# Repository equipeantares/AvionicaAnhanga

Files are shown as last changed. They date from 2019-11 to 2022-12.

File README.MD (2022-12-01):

# Base de Acionamento

## Introdução 

### Motivação

A equipe Antares de espaçomodelismo da Unicamp tem como um de seus projetos desenvolvidos o foguete Aurora. Trata-se de um foguete de propulsão sólida com apogeu esperado de 3km. Como parte dos requisitos necessários para ter sucesso na missão, o foguete precisa de um sistema de aviônica que será responsável por coletar dados e tomar decisões previamente programadas durante o voo. Com o objetivo de monitorar o estado do foguete antes, durante e depois do lançamento, é necessário ter um sistema em solo que seja capaz de receber os dados coletados pela aviônica, permitindo que os presentes tenham informações em tempo real. Além disso, esse sistema deve permitir que o acionador do motor seja ligado de forma segura durante o lançamento, não expondo pessoas a riscos.

### Objetivo

Sendo assim, o objetivo deste projeto é desenvolver um sistema de controle de base para o foguete, o qual deve ser capaz de iniciar o lançamento de forma segura e robusta e capaz de receber e apresentar dados da telemetria do voo colhidos pela aviônica.

### Soluções comerciais

Pelo fato de o sistema precisar ser personalizado, se ajustando ao sistema presente no foguete e aos demais requisitos específicos do projeto, não existem alternativas comerciais que cumpram integralmente o objetivo.

## Especificação
    - Microcontrolador: o dispositivo deverá ser capaz de fazer processamentos lógicos, sendo assim necessário um microcontrolador. Por motivos de acessibilidade e familiaridade, será utilizada a plataforma Arduino no MCU ESP-8266 12F.

    - Comunicação e dados: com o objetivo de receber dados de telemetria do foguete, o dispositivo deverá ter um sistema transceptor, que será implementado por um módulo LoRA E32-915T20D.

    - Interface: como interface, o dispositivo contará com pinos auxiliares para monitoramento do funcionamento da placa e pinos de seleção de função para alimentação e modo de acionamento da ignição, sendo a seleção feita por meio de jumpers.

    - Ignição: deverá suportar dois modos de acionamento do circuito ignitor: por sinal elétrico e por comando remoto. O modo será escolhido via inserção manual de jumpers antes do lançamento.

    - Alimentação: o sistema deverá ter interface de alimentação, podendo operar com a alimentação interna de 3V3 ou alimentação externa de 5V.

## Diagrama

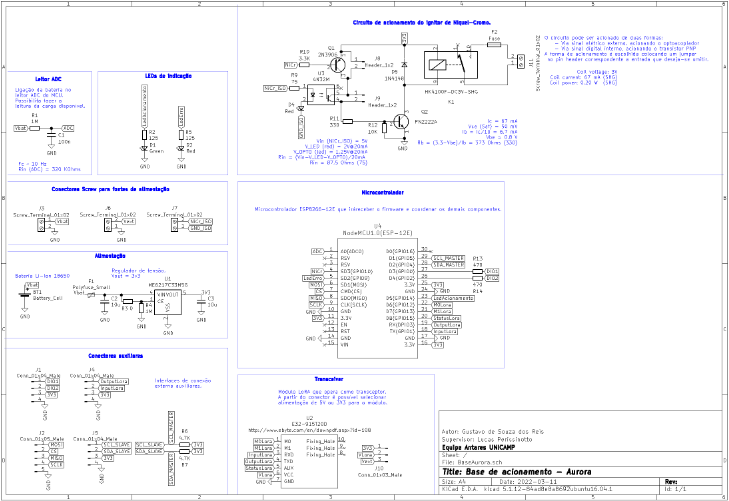
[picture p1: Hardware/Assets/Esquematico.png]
Esquematico


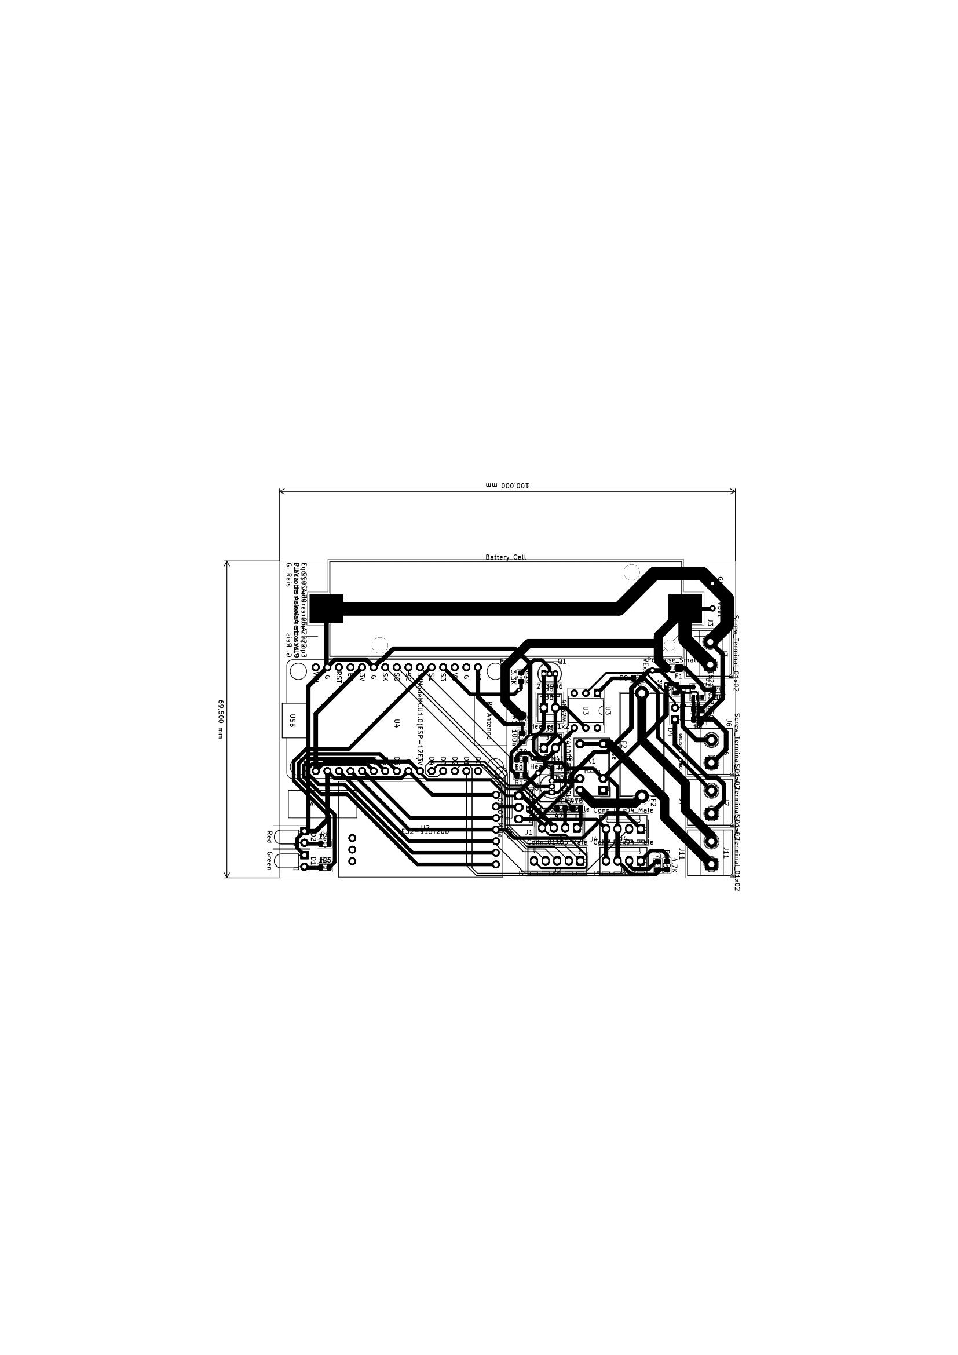
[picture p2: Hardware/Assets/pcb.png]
Layout PCB


## Pinagem

### Pinout conector Screw bateria 18650

Pino | Sinal
-----|------
1  | VBat
2  | GND

### Pinout conector Screw do Acionamento

Pino | Sinal
-----|------
  1  | NiCr_ISO
  2  | GND_ISO

### Pinout conector Screw Alimentação externa

Pino | Sinal
-----|------
  1  | VExt
  2  | GND

### Pinout conector GPIO aux

Pino | Sinal
-----|------
  1  | DIO1
  2  | DIO2
  3  | 3V3
  4  | GND

### Pinout conector LoRA aux

Pino | Sinal
-----|------
  1  | OutputLora
  2  | InputLora
  3  | 3V3
  4  | GND

### Pinout conector I2C aux

Pino | Sinal
-----|------
  1  | SCL_SLAVE
  2  | SDA_SLAVE
  3  | 3V3
  4  | GND

### Pinout conector SPI aux

Pino | Sinal
-----|------
  1  | MOSI
  2  | CS
  3  | MISO
  4  | SCLK
  5  | GND

### Pinout conector de seleção alimentação LoRA

Pino | Sinal
-----|------
  1  | 3V3
  2  | VLora
  3  | VExt

### Pinout conector Transistor PNP acionamento (interno)

Pino | Sinal
-----|------
  1  | Emissor
  2  | Coletor

### Pinout conector Optoacoplador acionamento (externo)

Pino | Sinal
-----|------
  1  | Coletor
  2  | Emissor

## Testes

    A fim de garantir que o sistema seja seguro e que tudo funcione como esperado, é necessário realizar testes controlados de cada parte do sistema, tentando antecipar possíveis falhas que possam ocorrer. 
    Como o sistema de ignição não pode ter acionamento indesejado, devem ocorrer testes em ambientes adversos, como, por exemplo, com componentes desconectados, e o resultado esperado é que o sistema não ative em nenhuma dessas situações.

## Relatório de funcionamento
	Durante o desenvolvimento do projeto foram encotradas algumas falhas que devem ser corrigidas na próxima versão da aviônica. A primeira delas é referente a pinagem do SPI, que estão incorretamente conectadas nos pinos de flash do microcontrolador, de forma que o módulo do cartão SD não funcione como desejado.
	 A segunda falha é o pino do buzzer, que é um pino que é usado para o boot da placa. Isso faz com que o buzzer fique ativado por todo o tempo durante o upload do código, tornando o processo de desenvolvimento do projeto um tanto irritante. Além disso, ocorreram erros por usar esse pino como saída no código, então, para uma próxima atualização do projeto, seria interessante utilizar uma outra GPIO diferente da 9 para operar este dispositivo.
	 Uma outra melhoria que pode ser feita no projeto é repensar o sitema da ignição da recuperação. A utilização de um dispositivo eletromecânico como o relê faz com que possa haver um acionamento indesejado devido à aceleração e movimentação do foguete. Sendo assim, seria mais seguro utilizar um circuito de acionamento digital, utilizando MOSFETs. Além disso, seria interessante implementar um circuito que fosse capaz de identificar a presença ou não do ignitor. Algo assim foi desenvolvido anteriormente pela equipe e o projeto pode ser acessado nas documentações antigas.

Relatório desenvolvido por: Gustavo S. Reis em 01/12/2022

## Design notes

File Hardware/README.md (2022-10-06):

# Projeto de Aviônica Icaro_II

Última atualização feita por Gustavo Reis (gustavosr8@gmail.com)

## Introdução 

### Motivação

A equipe Antares de espaçomodelismo da Unicamp tem como um de seus projetos desenvolvidos o foguete Anhangá. Trata-se de um foguete de propulsão sólida com apogeu esperado de 1km. Como parte dos requisitos necessários para ter sucesso na missão, o foguete precisa de um sistema de aviônica que será responsável por coletar dados e tomar decisões previamente programadas durante o voo. 

### Objetivo

Sendo assim, o objetivo deste projeto é desenvolver um sistema embarcado para o foguete, capaz de captar dados referentes ao voo, armazenar esses dados de forma segura e tomar decisões baseadas nas leituras feitas.

### Soluções comerciais

Pelo fato de o sistema precisar ser personalizado, se ajustando ao sistema presente no foguete e aos demais requisitos específicos do projeto, não existem alternativas comerciais que cumpram integralmente o objetivo.

## Especificação
    - Microcontrolador: o dispositivo deverá ser capaz de fazer processamentos lógicos, sendo assim necessário um microcontrolador. Por motivos de acessibilidade e familiaridade, será utilizada a plataforma Arduino no MCU ESP-8266 12F.

    - Dados: com o objetivo de receber dados de telemetria do foguete e armazená-los de forma segura, será utilizado um módulo para cartão micro SD e um cartão de 16GB.

    - Interface: como interface, o dispositivo contará com pinos auxiliares para monitoramento do funcionamento da placa e pinos de seleção de função para alimentação e modo de acionamento da ignição, sendo a seleção feita por meio de jumpers.

    - Ignição: deverá suportar dois modos de acionamento do circuito ignitor: por sinal elétrico e por comando remoto. O modo será escolhido via inserção manual de jumpers antes do lançamento.

    - Alimentação: o sistema deverá ter interface de alimentação, podendo operar com a alimentação interna de 3V3 ou alimentação externa de 5V.

## Testes

    A fim de garantir que o sistema seja seguro e que tudo funcione como esperado, é necessário realizar testes controlados de cada parte do sistema, tentando antecipar possíveis falhas que possam ocorrer. 
    Como o sistema de ignição não pode ter acionamento indesejado, devem ocorrer testes em ambientes adversos, como, por exemplo, com componentes desconectados, e o resultado esperado é que o sistema não ative em nenhuma dessas situações.

## Considerações e melhorias futuras

O sistema foi implementado e integrado no foguete Aurora I, para a LASC 2022. A captura de dados se mostrou muito robusta e o sistema de filtragem destes se demonstrou eficiente. A alimentação também teve um bom desempenho (foram utilizadas 2 baterias 18650 para iginição e uma do mesmo tipo para alimentação da placa) e podem até ser estudadas opções de desempenho energético inferior, porém com menor massa. Como pontos negativos para futuras melhorias cabe destacar a pinagem do buzzer, que era em um pino que se ativava sempre que o microcontrolador bootava, tornando o processo de desenvolvimento e debug um tanto desagradável dado o som estridente do dispositivo. O uso de um relay como acionador da ignição também é um ponto negativo do projeto, já que é um dispositivo eletro-mecânico, e, em presença de muito movimento e alta aceleração, como acontece no foguete, pode ocorrer um acionamento indesejado, causando a falha da missão. Uma solução para isso pode ser implementar um acionamento digital via MOSFET. Um último ponto a ser melhorado é a questão da redundância para garantir o sucesso da missão. Esse problema não tem tem uma solução trivial, e deve ser estudado.

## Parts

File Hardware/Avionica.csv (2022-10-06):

Source: | /home/gustavo/Área de Trabalho/Unicamp/Antares/KiCad/Projetos/Avionica/Irapuru-II/Avionica.sch
Date: | Seg 25 Abr 2022 16:16:38 -03
Tool: | Eeschema 5.1.12-84ad8e8a86~92~ubuntu16.04.1
Generator: | /usr/share/kicad/plugins/bom_csv_grouped_by_value_with_fp.py
Component Count: | 35
Ref | Qnty | Value | Cmp name | Footprint | Description | Vendor
A1, | 1 | BMP280_Module | BMP280_Module | CharlesLabs:BMP280_Module
A2, | 1 | SD_Card_Module | SD_Card_Module | CharlesLabs:SD_Card_Module
BZ1, | 1 | Buzzer | Buzzer | Buzzer_Beeper:Buzzer_12x9.5RM7.6 | Buzzer, polarized
C1, | 1 | 100n | C_Small | Capacitor_SMD:C_0805_2012Metric | Unpolarized capacitor, small symbol
C2, C3, | 2 | 10u | C_Small | Capacitor_SMD:C_0805_2012Metric | Unpolarized capacitor, small symbol
D1, D4, | 2 | Green | LED_Small | LED_THT:LED_D3.0mm | Light emitting diode, small symbol
D2, | 1 | Red | LED_Small | LED_THT:LED_D3.0mm | Light emitting diode, small symbol
D3, | 1 | 1N4148 | D_Small | Diode_SMD:D_SOD-123 | Diode, small symbol
F1, | 1 | Polyfuse_Small | Polyfuse_Small | Fuse:Fuse_1206_3216Metric_Castellated | Resettable fuse, polymeric positive temperature coefficient, small symbol
F2, | 1 | Fuse | Fuse | Fuse:Fuseholder_Cylinder-5x20mm_Stelvio-Kontek_PTF78_Horizontal_Open | Fuse
J1, J2, J5, | 3 | Screw_Terminal_01x02 | Screw_Terminal_01x02 | TerminalBlock_Phoenix:TerminalBlock_Phoenix_MKDS-1,5-2_1x02_P5.00mm_Horizontal | Generic screw terminal, single row, 01x02, script generated (kicad-library-utils/schlib/autogen/connector/)
J3, J4, | 2 | Header_1x2 | Conn_01x02_Male | Connector_Molex:Molex_KK-254_AE-6410-02A_1x02_P2.54mm_Vertical | Generic connector, single row, 01x02, script generated (kicad-library-utils/schlib/autogen/connector/)
K1, | 1 | HK4100F-DC3V-SHG | G5V-1 | Relay_THT:Relay_SPDT_HJR-4102 | Ultra-miniature, Highly Sensitive SPDT Relay for Signal Circuits
Q1, | 1 | 2N3906 | 2N3906 | Package_TO_SOT_THT:TO-92_Inline | -0.2A Ic, -40V Vce, Small Signal PNP Transistor, TO-92
Q2, | 1 | PN2222A | PN2222A | Package_TO_SOT_THT:TO-92_Inline | 1A Ic, 40V Vce, NPN Transistor, General Purpose Transistor, TO-92
R1, R5, | 2 | 1M | R_Small | Resistor_SMD:R_0805_2012Metric | Resistor, small symbol
R2, R3, | 2 | 4.7K | R_Small | Resistor_SMD:R_0805_2012Metric | Resistor, small symbol
R4, | 1 | 0 | R_Small | Resistor_SMD:R_0805_2012Metric | Resistor, small symbol
R6, R12, | 2 | 125 | R_Small | Resistor_SMD:R_0805_2012Metric | Resistor, small symbol
R7, | 1 | 75 | R_Small | Resistor_SMD:R_0805_2012Metric | Resistor, small symbol
R8, | 1 | 3.3K | R_Small | Resistor_SMD:R_0805_2012Metric | Resistor, small symbol
R9, | 1 | 330 | R_Small | Resistor_SMD:R_0805_2012Metric | Resistor, small symbol
R10, | 1 | 10K | R_Small | Resistor_SMD:R_0805_2012Metric | Resistor, small symbol
R11, | 1 | 100 | R_Small | Resistor_SMD:R_0805_2012Metric | Resistor, small symbol
U1, | 1 | ME6217C33M5G | ME6217C33M5G-BaseAurora | Package_TO_SOT_SMD:SOT-23-5
U2, | 1 | 4N32M | 4N25 | Package_DIP:DIP-6_W7.62mm | DC Optocoupler Base Connected, Vce 30V, CTR 20%, Viso 2500V, DIP6
U3, | 1 | NodeMCU1.0(ESP-12E) | NodeMCU1.0(ESP-12E) | ESP8266:ESP12F-Devkit-V3

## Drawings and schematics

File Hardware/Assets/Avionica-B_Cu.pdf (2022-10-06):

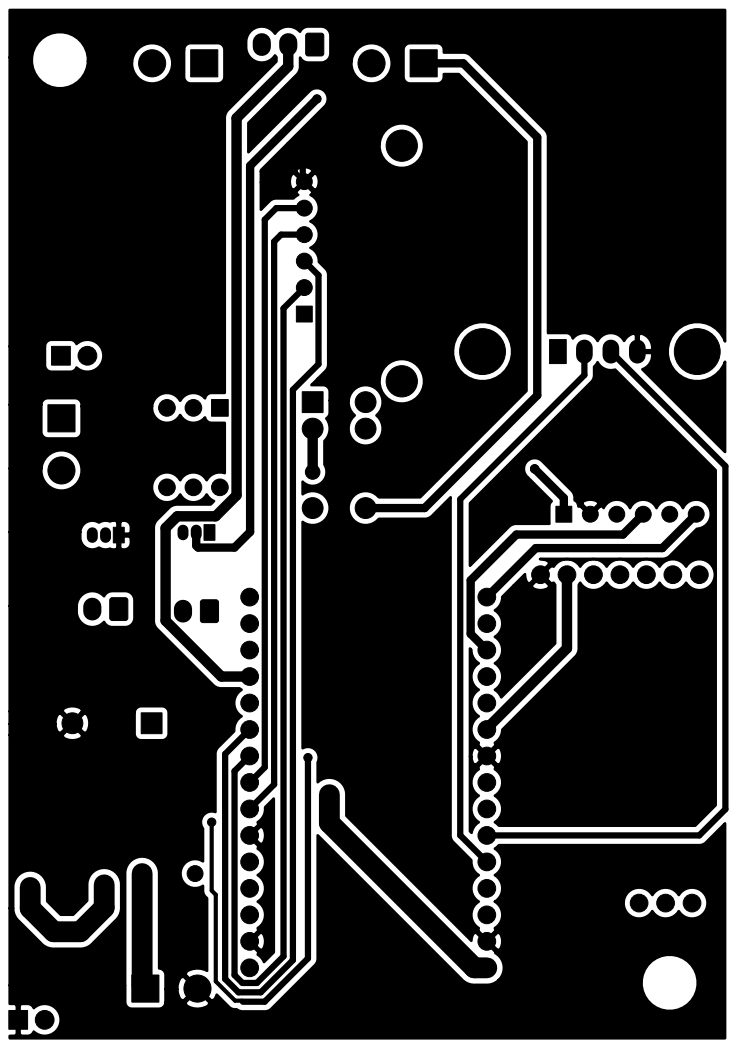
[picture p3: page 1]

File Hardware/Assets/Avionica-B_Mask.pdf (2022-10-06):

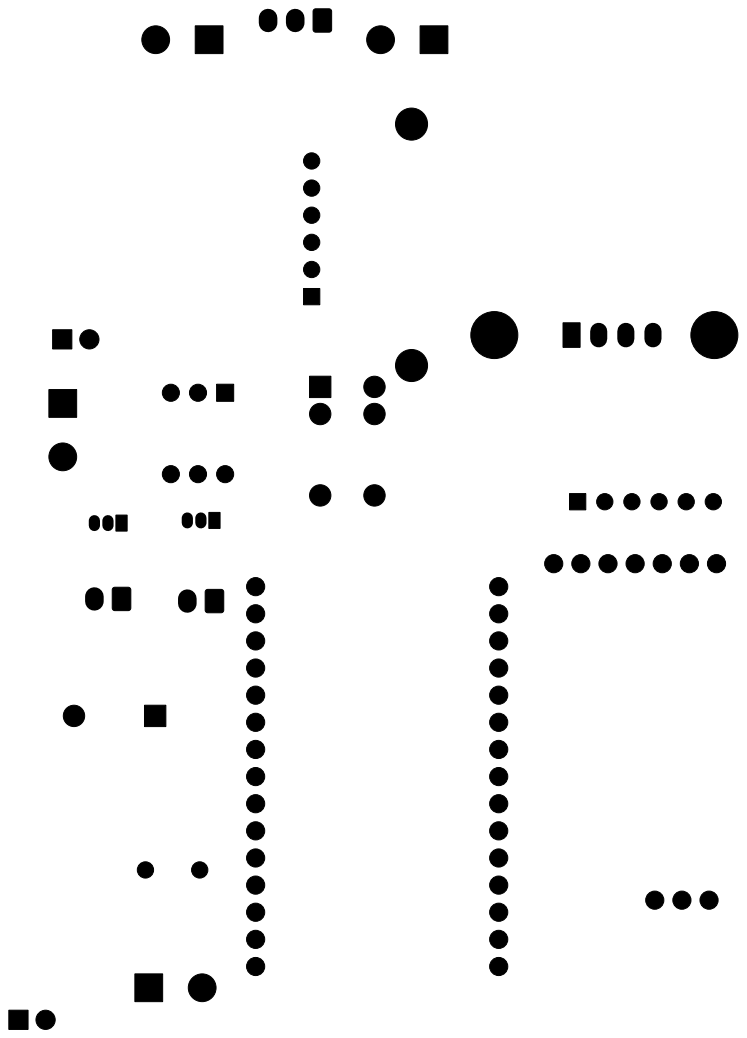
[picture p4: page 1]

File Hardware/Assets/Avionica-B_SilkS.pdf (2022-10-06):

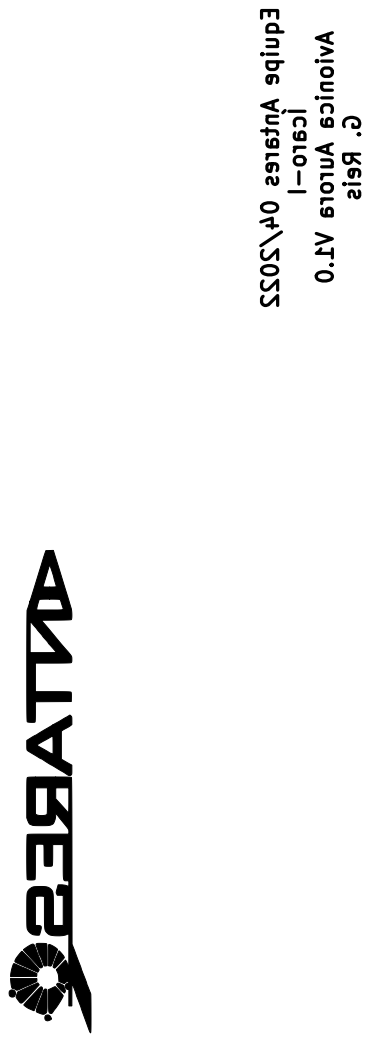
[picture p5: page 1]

Equipe Antares 04/2022 Ícaro-I Avionica Aurora V1.0 G. Reis

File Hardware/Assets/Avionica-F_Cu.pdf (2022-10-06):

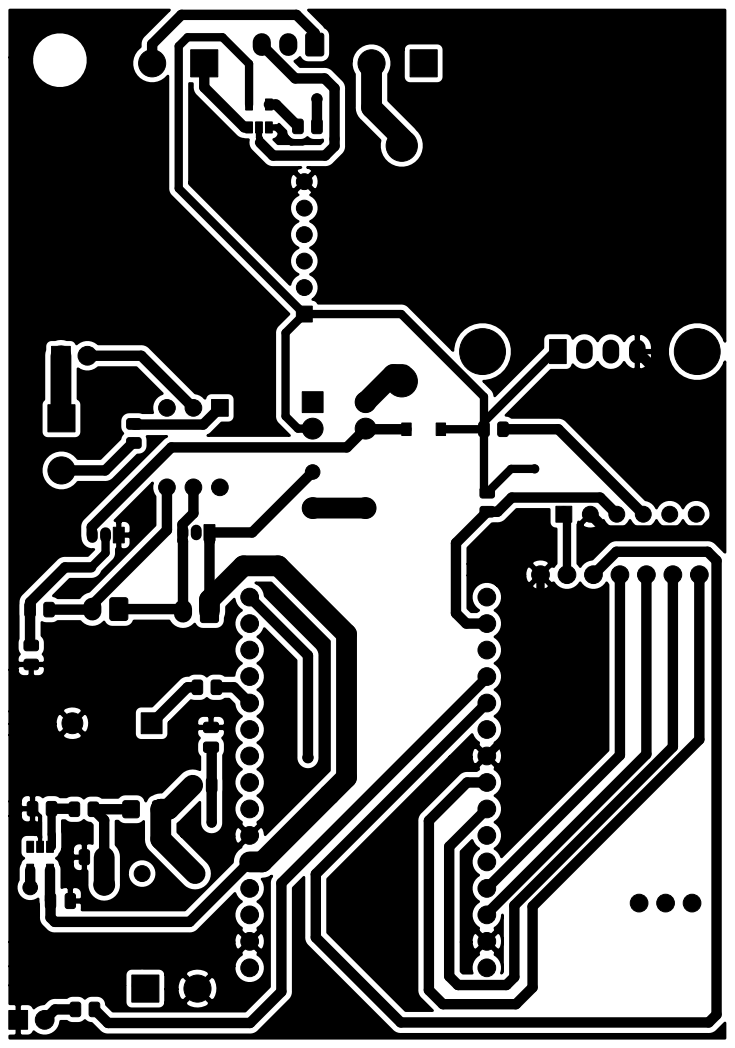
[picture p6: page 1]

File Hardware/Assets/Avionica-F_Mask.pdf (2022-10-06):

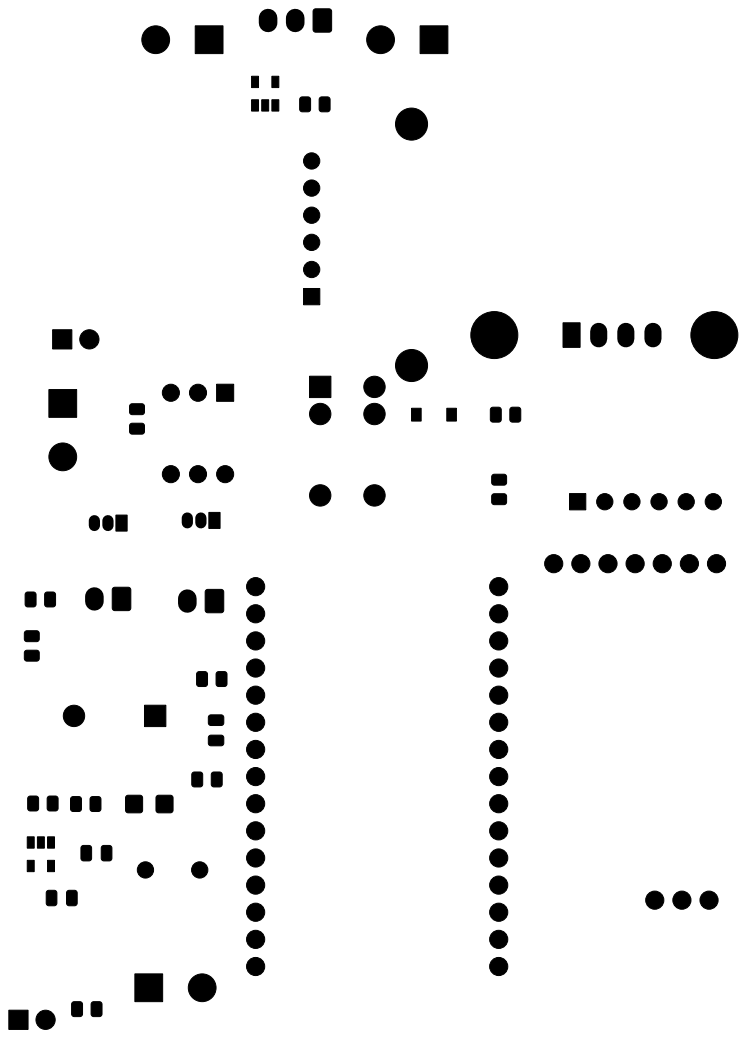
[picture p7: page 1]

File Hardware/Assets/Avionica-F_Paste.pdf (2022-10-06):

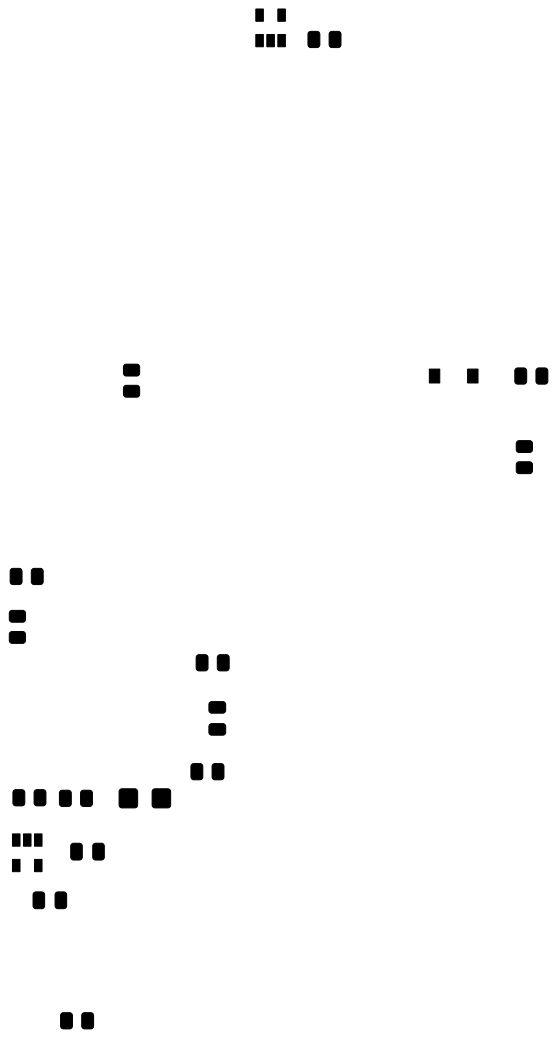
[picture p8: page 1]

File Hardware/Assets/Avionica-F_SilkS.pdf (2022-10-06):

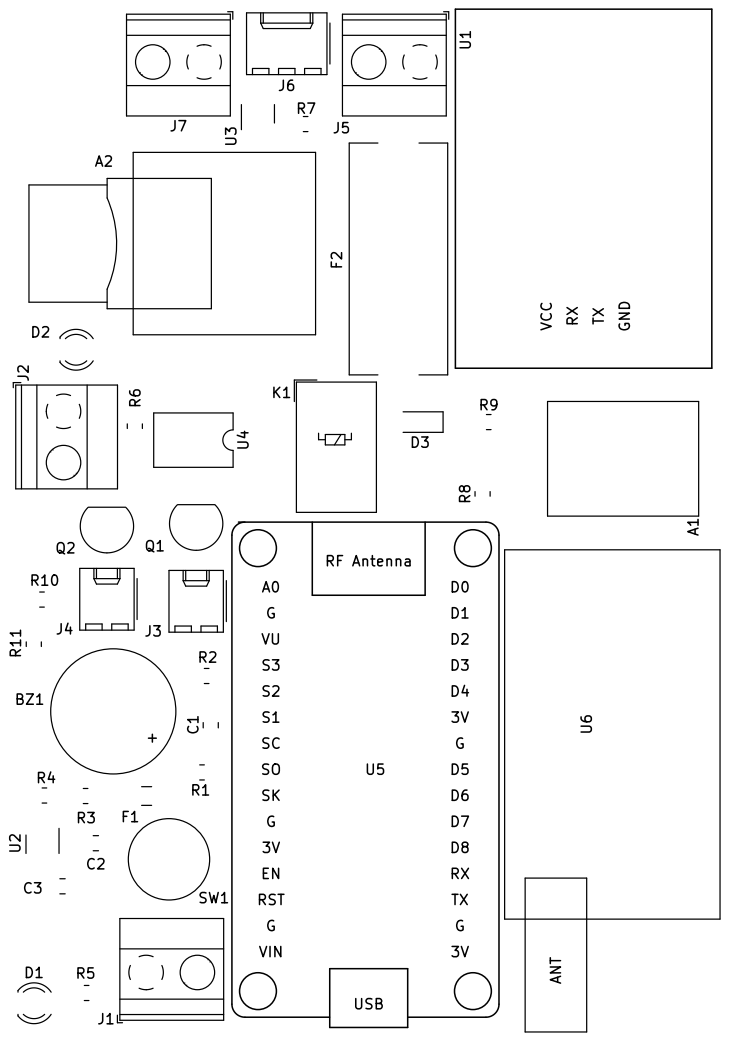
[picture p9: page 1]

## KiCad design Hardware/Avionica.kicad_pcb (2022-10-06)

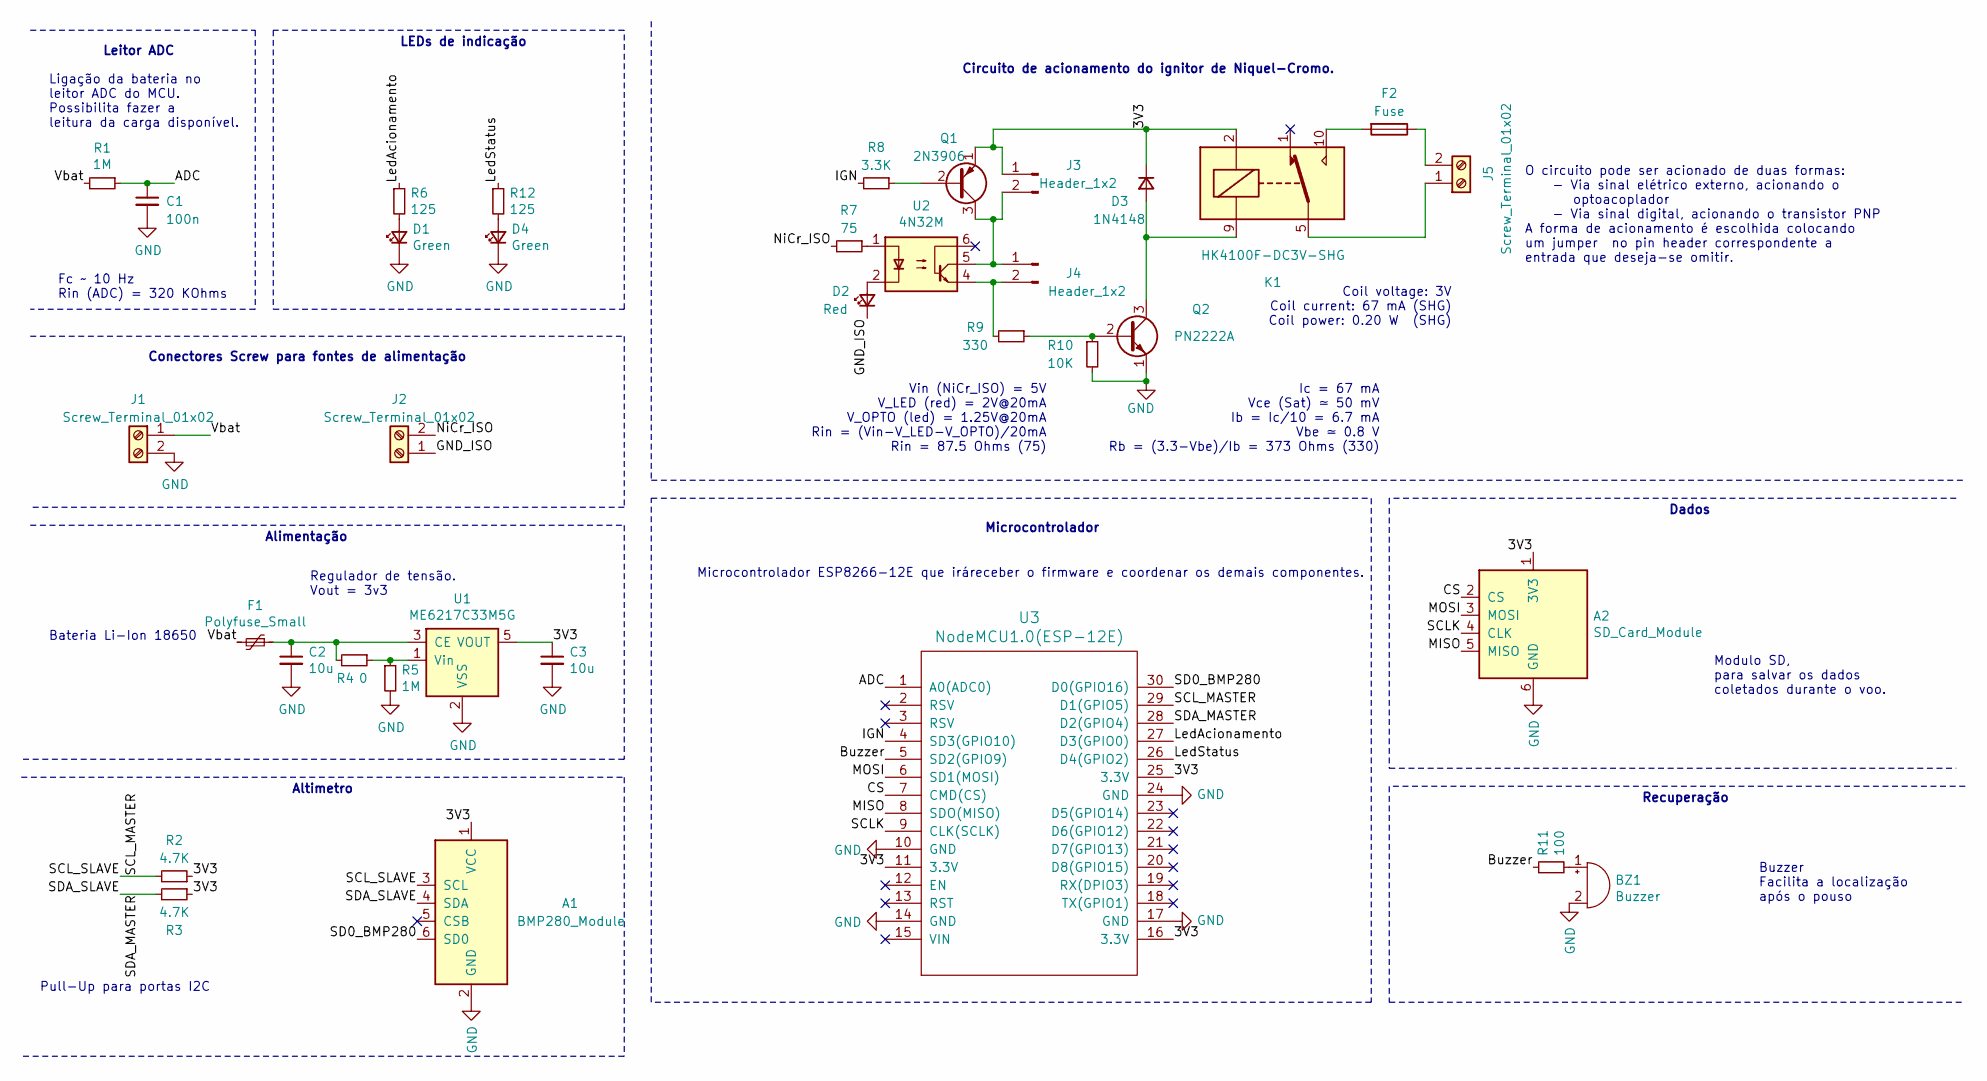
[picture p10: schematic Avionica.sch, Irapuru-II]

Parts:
A1: BMP280_Module
A2: SD_Card_Module
BZ1: Buzzer; Buzzer_12x9.5RM7.6
C1: 100n; C_0805_2012Metric
C2, C3: 10u; C_0805_2012Metric
D1, D4: Green; LED_D3.0mm
D2: Red; LED_D3.0mm
D3: 1N4148; D_SOD-123
F1: Polyfuse_Small; Fuse_1206_3216Metric_Castellated
F2: Fuse; Fuseholder_Cylinder-5x20mm_Stelvio-Kontek_PTF78_Horizontal_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
J1, J2, J5: Screw_Terminal_01x02; TerminalBlock_Phoenix_MKDS-1,5-2_1x02_P5.00mm_Horizontal
J3, J4: Header_1x2; Molex_KK-254_AE-6410-02A_1x02_P2.54mm_Vertical
K1: HK4100F-DC3V-SHG; Relay_SPDT_HJR-4102
Q1: 2N3906; TO-92_Inline
Q2: PN2222A; TO-92_Inline
R1, R5: 1M; R_0805_2012Metric
R2, R3: 4.7K; R_0805_2012Metric
R4: 0; R_0805_2012Metric
R6, R12: 125; R_0805_2012Metric
R7: 75; R_0805_2012Metric
R8: 3.3K; R_0805_2012Metric
R9: 330; R_0805_2012Metric
R10: 10K; R_0805_2012Metric
R11: 100; R_0805_2012Metric
U1: ME6217C33M5G; SOT-23-5
U2: 4N32M; DIP-6_W7.62mm
U3: NodeMCU1.0(ESP-12E); ESP12F-Devkit-V3

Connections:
/3V3: A1.1 (VCC), A2.1 (3V3), C3.1, D3.1 (K), J3.1, K1.2, Q1.1 (E), R2.1, R3.1, U1.5 (VOUT), U3.11 (3.3V), U3.16 (3.3V), U3.25 (3.3V)
/ADC: C1.1, R1.1, U3.1 (A0(ADC0))
/Buzzer: R11.1, U3.5 (SD2(GPIO9))
/CS: A2.2 (CS), U3.7 (CMD(CS))
/GND_ISO: D2.1 (K), J2.1
/IGN: R8.2, U3.4 (SD3(GPIO10))
/LedAcionamento: R6.1, U3.27 (D3(GPIO0))
/LedStatus: R12.1, U3.26 (D4(GPIO2))
/MISO: A2.5 (MISO), U3.8 (SDO(MISO))
/MOSI: A2.3 (MOSI), U3.6 (SD1(MOSI))
/NiCr_ISO: J2.2, R7.2
/SCLK: A2.4 (CLK), U3.9 (CLK(SCLK))
/SCL_MASTER: A1.3 (SCL), R2.2, U3.29 (D1(GPIO5))
/SD0_BMP280: A1.6 (SD0), U3.30 (D0(GPIO16))
/SDA_MASTER: A1.4 (SDA), R3.2, U3.28 (D2(GPIO4))
/Vbat: F1.2, J1.1, R1.2
GND: A1.2 (GND), A2.6 (GND), BZ1.2 (+), C1.2, C2.2, C3.2, D1.1 (K), D4.1 (K), J1.2, Q2.1 (E), R5.2, R10.2, U1.2 (VSS), U3.10 (GND), U3.14 (GND), U3.17 (GND), U3.24 (GND)
unnamed: BZ1.1 (-), R11.2
unnamed: C2.1, F1.1, R4.2, U1.3 (CE)
unnamed: D1.2 (A), R6.2
unnamed: D2.2 (A), U2.2
unnamed: D3.2 (A), K1.9, Q2.3 (C)
unnamed: D4.2 (A), R12.2
unnamed: F2.1, J5.2
unnamed: F2.2, K1.10
unnamed: J3.2, J4.1, Q1.3 (C), U2.5
unnamed: J4.2, R9.2, U2.4
unnamed: J5.1, K1.5, K1.6
unnamed: Q1.2 (B), R8.1
unnamed: Q2.2 (B), R9.1, R10.1
unnamed: R4.1, R5.1, U1.1 (Vin)
unnamed: R7.1, U2.1

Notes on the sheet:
Coil voltage: 3V Coil current: 67 mA (SHG) Coil power: 0.20 W (SHG)
Fc ~~ 10 Hz Rin (ADC) = 320 KOhms
Conectores Screw para fontes de alimentação
LEDs de indicação
Ligação da bateria no leitor ADC do MCU. Possibilita fazer a leitura da carga disponível.
Microcontrolador ESP8266-12E que iráreceber o firmware e coordenar os demais componentes.
O circuito pode ser acionado de duas formas: - Via sinal elétrico externo, acionando o optoacoplador - Via sinal digital, acionando o transistor PNP A forma de acionamento é escolhida colocando um jumper no pin header correspondente a entrada que deseja-se omitir.
Microcontrolador
Dados
Alimentação
Leitor ADC
Circuito de acionamento do ignitor de Niquel-Cromo.
Ic = 67 mA Vce (Sat) ≃ 50 mV Ib = Ic/10 = 6.7 mA Vbe ≃ 0.8 V Rb = (3.3-Vbe)/Ib = 373 Ohms (330)
Vin (NiCr_ISO) = 5V V_LED (red) = 2V@20mA V_OPTO (led) = 1.25V@20mA Rin = (Vin-V_LED-V_OPTO)/20mA Rin = 87.5 Ohms (75)
Recuperação
Altimetro
Pull-Up para portas I2C
Modulo SD, para salvar os dados coletados durante o voo.
Buzzer Facilita a localização após o pouso
Regulador de tensão. Vout = 3v3
Bateria Li-Ion 18650

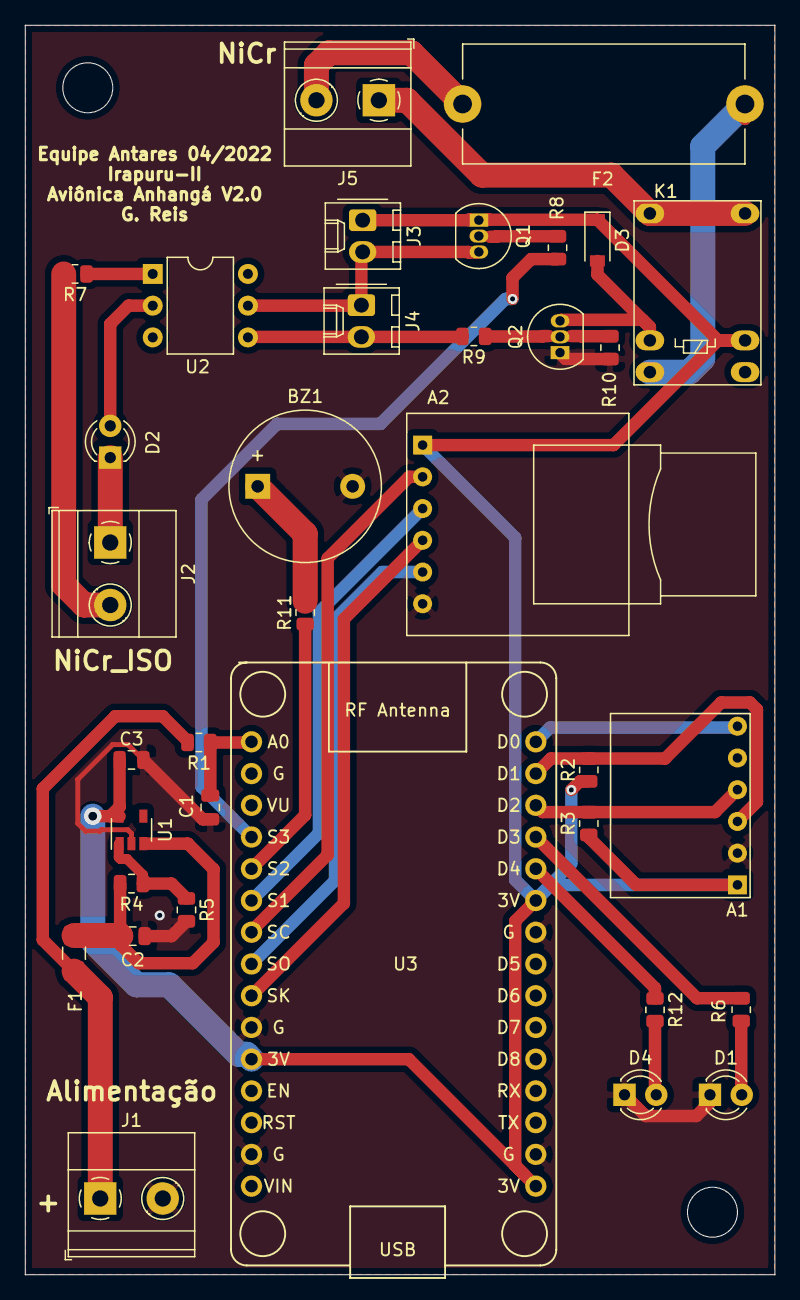
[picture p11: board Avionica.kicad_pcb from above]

Board: 2 copper layers, 60.0 x 100.0 mm, 35 parts (0 on the bottom side), 32 nets.

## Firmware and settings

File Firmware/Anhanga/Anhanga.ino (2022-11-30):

/***************************************************************************
  ------------- Embedded firmware for LASC 2021/2022 -----------------
  Authors: Batata, Joan, Gabriel
  Adapted by: Andre, Reis
  Version: 3.0 - 08/2022
  Description:
    This firmware implements a state machine, keeping track of the rocket
    flight phases and acting accordingly.
    There are 6 main flight states:
      E1 - Ground before launch
      E2 - Propulsive flight
      E3 - Ballistic flight
      E4 - Descent with parachute
      E5 - Ground after flight
      E10- Failure mode
    Between each of these states, there are main transitions and actions 
    on the rocket, the parachute launch being the most important one.
    
    The rocket phases and state transitions, as well as the fluxogram of this
    code are presented in detail in the firmware development report, located 
    in Antares Google drive repository.
  
 ***************************************************************************/

/*  TODO:
 *   - Implement sea pressure definition at startup   5
 *   - Implement burning finish condition             7   
 */

/* ----- Library Inclusion ----- */

#include <Wire.h>
#include <Adafruit_BMP280.h>
#include <SD.h>
#include <SPI.h>
#include <Ticker.h>
#include "voo.h"


/* ----- Macro definitions ----- */

#define IGN           10        // I/O pin for ignitor digital output
#define BUZZ          9         // I/O pin for buzzer digital output
#define PWR_READ      A0        // I/O pin for analogic power read
#define ADD_BMP       0x76      // Address of BMP
#define TIMER_TKS     500       // Timer ticks in a period (Timer runs at 5MHz freq.) - [500 for period of 0.1ms]
#define T_MEASURE     56        // Measure period (x 0.1ms) - [56 for 181.8 Hz]
#define DELTA_H_FLY   50.0      // Height difference with respect to the launch site for flight condition [m]
#define DELTA_H_LAND  20.0      // Height difference with respect to the launch site for landing condition [m]
#define DELTA_V_FLY   20.0      // Minimum velocity for flight condition [m/s]
#define DELTA_T_BURN  4.0       // Minimum time after lift-off from which we begin looking for apogee condition [s]
#define T_MAX_IGN     20.0      // Maximum time after lift-off from which we activate parachute no matter what [s]
#define BLUE_LED      0         // Digital output blue led for debbugin
#define GREEN_LED     2         // Digital output green led for debbugin
#define V0            15.0      // Velocity to trigger apogee condition [m/s]
#define V0_MARGIN     0.2       // Margin [%] around V0 value
#define CS_PIN        15        // Chip Select pin - SPI for SD


/* ----- Constant definitions ----- */

const byte chipSelect = CS_PIN;         // Chip Select pin for SPI communication with SD card
const int initialHeight = 645;            // Initial height for getting sea level pressure [m]
const String dFileName = "antares.txt";   // Data filename in SD  

/* ----- Global variables definitions ----- */

volatile unsigned long timeCount = 0UL;   // A long is 32 bits long = 4294967296 levels
                                          // Using a dt=100us, it can count up to 119 hours
volatile unsigned int measureCount = 0;   // Counter for dividing timer freq. to get measure freq.
volatile unsigned int delayCount = 0;     // Counter for dividing measureCount to get delays
volatile byte state = 0;                  // State of the flight (E1 corresponds to 0, and so forth)
volatile bool led_on = false;             // Variable for test LED state

Ticker timer;                             // Object used as interrupt timer
Adafruit_BMP280 bmp;                      // Object used as BMP280 driver - I2C use
Voo voo = Voo(0.0056, 1.0);               // Object containing height, velocity, acceleration - sensor 
volatile unsigned long timeSave = 0UL;    // Variable used for storing moment of last measure of sensor 
volatile unsigned long timeLiftOff = 0UL; // Variable used for storing lift-off moment
volatile float bmpPi;                     // Initial pressures on sensor
volatile float bmpHi;                     // Initial height measured on sensor
volatile float bmpDi;                      // Derivative of height w.r.t. pressure on initial pressure 



/* ----- Auxiliary function definitions ----- */

/* Timer 1 Interruption Sub-Routine for AVR1*/
/*
ISR(TIMER1_COMPA_vect){
  timeCount++;                    // Increments time counter
  measureCount++;                 // Increments measure counter
  if(measureCount == T_MEASURE){  // 5600us makes a period of 181.8Hz
    measureCount = 0;             // Reset measure counter for main program
    delayCount++;
  }
}
*/

/* Timer Interruption Sub-Routine for ESP8266 */
void ICACHE_RAM_ATTR onTime() {
  timeCount++;
  measureCount++;
  if(measureCount == T_MEASURE){  // 5600us makes a period of 181.8Hz
    measureCount = 0;             // Reset measure counter for main program
    delayCount++;
  }
}



/* Get present time in seconds */
float get_time(){
  noInterrupts();
  float t = timeCount/10000.0;
  interrupts();
  return(t);
}


/* Save data to SD function */
void save_to_SD(Voo dados){
  File dataFile;                                        // Object used as SD driver - SPI use
//  Serial.println(F("Dados de altura internos:"));
  int vsize = 6;
  float fVect [vsize] = {get_time(),                    // Time since start-up in seconds
                        dados.pressao,                  // Last acquired pressure [hPa]
                        dados.altura.getValor(0),       // Last acquired height measure [m]
                        dados.alturaF.getValor(0),      // Last acquired filtered height measure [m]
                        dados.velocidade.getValor(0),   // Last acquired velocity measure [m/s]
                        dados.velocidadeF.getValor(0)   // Last acquired flitered velocity measure [m/s]                    
  };
  byte sVect [1] = {state};                              // State of the flight
         
  dataFile = SD.open(dFileName, FILE_WRITE);
  if(!dataFile){
    Serial.println(F("---> ERRO na abertura do arquivo"));
  }
;
  for(int i=0; i<vsize; i++){
    dataFile.print(F("\t"));
    dataFile.print(fVect[i]);
    Serial.print(F("\t"));
    Serial.print(fVect[i],1);
  }
  for(int i=0; i<2; i++){
    dataFile.print(F("\t"));
    dataFile.print(sVect[i]);
    Serial.print(F("\t"));
    Serial.print(sVect[i]);
  }
  dataFile.print(F("\n"));
  Serial.print(F("\n"));
  dataFile.close();
  return;
}

/* BMP height configuration - call on setup */
bool configure_BMP(){
  
  bmpPi = 0;
  bmpHi = 0;
  bmpDi = 0;
  int address = ADD_BMP;                                        // Gets bmp adress accordingly
  //Adafruit_BMP280 * bmpHandle = bmp;                          // Gets bmp object handle accordingly
  if (!bmp.begin(0x76)) {                                       // Initialize BMP
    Serial.print(F("Could not find BMP280 sensor (add="));
    Serial.print(address);
    Serial.println(F("), check wiring and reset!"));
    return(false);
  }
  bmp.setSampling(Adafruit_BMP280::MODE_NORMAL,        /* Operating Mode. */
                  Adafruit_BMP280::SAMPLING_X1,               /* Temp. oversampling */
                  Adafruit_BMP280::SAMPLING_X1,               /* Pressure oversampling */
                  Adafruit_BMP280::FILTER_OFF,                /* Filtering. */
                  Adafruit_BMP280::STANDBY_MS_1);             /* Standby time. */
  for(int i=0; i<100; i++){
    bmpPi += bmp.readPressure();                        // Read initial pressure [Pa]
    bmpHi += bmp.readAltitude();                        // Read initial altitude (exponential method) [m]
  }
  bmpPi = bmpPi/100.0;                                        // Get average of pressure in 100 measures [Pa]
  bmpHi = bmpHi/100.0;                                        // Get average of height in 100 measures [m]
  bmpPi /= 100.0;                                             // Transform pressure to hPa (divide by 100)
  bmpDi = -2260.209*pow(bmpPi,-0.8097);                       // Calculate derivative in initial pressure
  
  Serial.println(F("Finished configuration of BMP"));
  Serial.print(F("bmpPi = "));
  Serial.println(bmpPi,3);
  Serial.print(F("bmpHi = "));
  Serial.println(bmpHi,3);
  Serial.print(F("bmpDi = "));
  Serial.println(bmpDi,3);
  //File dataFile;
  
  return(true);
}

/* BMP height reading - Linear method */
float read_BMP_h(){
  
  float p,h;
  //Adafruit_BMP280 * bmpHandle = bmp;                            // Get bmp object handle accordingly
  //Voo * flightHandle = voo;                                     // Get flight object handle acconrdingly
  p = bmp.readPressure();                                // Read pressure [Pa]
  voo.pressao = p;                                    // Save in flight object
  p /= 100.0;                                                   // Transform pressure to hPa
//  h = 44330 * (1.0 - pow(p / 1013.25, 0.1903));               // Normal calculation of height
  h = bmpHi + bmpDi * (p - bmpPi);                              // Linearization of height
  return(h);
}

/* BMP average valid reading - call on loop */
float read_avg_BMP(){
  
  float read_h = 0.0;
  float acc_h = 0.0;
  byte measuresDone = 0;                                        // Counter for valid height acquisitions from sensors
  byte failed = 0;                                              // Counter for failed acquisitions from sensors
  while(measuresDone < 3 && failed < 3){     
    if(measureCount == 0){                                      // Waits cycle of measurement (acquisition frequency)
      read_h = read_BMP_h();
      if(read_h < 2000 && read_h > 0){                          // Measure validation: h in launch site is 645m + max of flight is 1000m = total of 1645m
        acc_h += read_h;                
        measuresDone++;
      }
      else
        failed++;
    }
  }
  if(failed >= 3){                                              // If the measure has failed more than 3 times, returns 0.
//    Serial.print(F("ERROR: BMP failed more than 3 times!"));
    return(0.0);
  }
  else
    return(acc_h/3.0);
}

/* Function to get time interval between sensor readings */
float get_dt(){
  unsigned long timeSave; 
  unsigned int deltaT;
  timeSave = timeSave;                                          // Get last saved time instant
  noInterrupts();                                               // Disable interrupts because of manipulation of timeCount
  deltaT = (unsigned int)(timeCount - timeSave);                // Effective dT calculation
  timeSave = timeCount;                                         // Update saved time instant
  interrupts();                                                // Re-enable interrupts
  return(deltaT/10000.0);
}

/* LED configuration - call on setup */
void LED_config(){ 
  pinMode(GREEN_LED, OUTPUT);
  digitalWrite(GREEN_LED, LOW);
  pinMode(BLUE_LED, OUTPUT);
  digitalWrite(BLUE_LED, LOW);
}

/* test routine*/
void Toggle(){
  digitalWrite(BUZZ, HIGH);
  digitalWrite(GREEN_LED, HIGH);
  delay(100);
  digitalWrite(BUZZ, LOW);
  digitalWrite(GREEN_LED, LOW);
  delay(400);
  digitalWrite(BUZZ, HIGH);
  digitalWrite(BLUE_LED, HIGH);
  delay(100);
  digitalWrite(BUZZ, LOW);
  digitalWrite(BLUE_LED, LOW);
}

/* Ignitor Analog reading - Get ignitor state */
/*
byte get_ignitor_state(){
  int value = analogRead(IGN_READ);
  float voltage = 5*value/1023.0;
  Serial.print(F("Voltage reading is = "));
  Serial.println(voltage,1);
  byte state;
  if(voltage > 0.9*IGN_V_OPEN && voltage < 1.1*IGN_V_OPEN){
     state = 0;
  }
  else if(voltage > 0.9*IGN_V_PRESENT && voltage < 1.1*IGN_V_PRESENT){
     state = 1;
  }
  else if(voltage < 2*IGN_V_ACTIVE){
     state = 2;
  }
  return(state);
}
*/

/* Identify Flight Condition */
bool flight_condition(){
  float h = voo.alturaF.getValor(0);
  float v = voo.velocidadeF.getValor(0);
  if( (h > bmpHi + DELTA_H_FLY && v > DELTA_V_FLY))
  {
    return(true);
  }
  else{
    return(false);
  }
}

/* Identify end of propulsion Condition */
bool burn_end_condition(){
  noInterrupts();
  int timeSinceLO = timeCount - timeLiftOff;
  interrupts();
  if(timeSinceLO/10000.0 > DELTA_T_BURN){
    return(true);
  }
  else{
    return(false);
  }
}

/* Identify Apogee Condition */
bool apogee_condition(){
  float v = voo.velocidadeF.getValor(0);
  noInterrupts();
  long timeSinceLO = timeCount - timeLiftOff;
  interrupts();
  if( ((1-V0_MARGIN)*V0 < v && v < (1+V0_MARGIN)*V0) ||
      timeSinceLO/10000.0 > T_MAX_IGN)
  {
    return(true);
  }
  else{
    return(false);
  }
}

/* Identify Landing Condition */
bool landing_condition(){
  float h = voo.alturaF.getValor(0);
  float v = voo.velocidade.getValor(0);
  if((h < bmpHi + DELTA_H_LAND && h > bmpHi - DELTA_H_LAND && v < DELTA_V_FLY))
  {
    return(true);
  }
  else{
    return(false);
  }
}

/*Create an header for the text file in the SD card*/
void Header(){
    File dataFile;                                        // Object used as SD driver - SPI use
//  Serial.println(F("Dados de altura internos:"));
         
  dataFile = SD.open(dFileName, FILE_WRITE);
  if(!dataFile){
    Serial.println(F("---> ERRO na abertura do arquivo"));
  }
  else {
      dataFile.print(F("\t"));
      dataFile.print(F("Time [s]"));
      dataFile.print(F("\t"));
      dataFile.print(F("Pressure [Pa]"));
      dataFile.print(F("\t"));
      dataFile.print(F("Height [m]"));
      dataFile.print(F("\t"));
      dataFile.print(F("fHeight [m]"));
      dataFile.print(F("\t"));
      dataFile.print(F("Velocity [m/s]"));
      dataFile.print(F("\t"));
      dataFile.print(F("fVelocity [m/s]"));
   }
}


/* ----- Setup function definition ----- */

void setup() {
  delay(5000);
  /* Serial communication Configuration */
  Serial.begin(9600);
  Serial.println(F("Anhanga Firmware Debugging..."));

  /* I/O Configuration */
  pinMode(IGN, OUTPUT);                                     // Configure ignitor pin as digital output
  digitalWrite(IGN, HIGH);                                  //The ignition pin activates as LOW, so it is initialized HIGH for safety reasons
  pinMode(BUZZ, OUTPUT);                                    // Configure buzzer pin as digital output
  pinMode(chipSelect, OUTPUT);                              // Configure Chip Select pin as digital output
  LED_config();                                             // Configure LED for testing code
  Serial.println(F("I/O configuration done."));
  Toggle();
  delay(1000);
  /* SD Configuration */
  if(!SD.begin(chipSelect)){ 
    Serial.println(F("Error in SD card configuration!"));
    state = 10;
    return;
  }
  else{
    Serial.println(F("SD configuration done."));
    Serial.print(F("Saving data in: "));
    Serial.println(dFileName);
    File dataFile;
    dataFile = SD.open(dFileName, FILE_WRITE);
    if(!dataFile){
      Serial.println(F("---> ERRO na abertura do arquivo"));
      state = 10;
      return;
    }
  Header();
    dataFile.println(F("\n"));
    dataFile.close();
  }
  Toggle();
  delay(1000);
  
  /* BMP280 Configuration */
  if(configure_BMP())                                       // Configuration and initialization funcions of BMP1 and BMP2
    Serial.println(F("BMP configuration done."));
  else{
    Serial.println(F("Problems on BMP configuration."));
    state = 10;
    return;
    }
  Toggle();
  delay(1000);
    
  /* Timer 1 (16-bit) configuration */
//  TCCR1A = 0x00;                                            // Configure timer on internal source and CTC (Clear Timer on Compare) match mode.
//  TCCR1B = B00001010;                                       // Configure internal clock with prescaler = 8 --> Timer frequency = 2MHz. 
//                                                            // Precise CTC mode - clear on OCR1A register match.
//  OCR1A = TIMER_TKS;                                        // Amount of timer ticks to generate period of 100us (10kHz).
//  Serial.println(F("Timer 1 configured."));
//  
//  /* Timer 1 Interruption configuration */
//  TIMSK1 |= 0x02;                                           // Enable Interrupt on OCR1A Match
//  interrupts();                                             // Enable interruptions

  timer1_attachInterrupt(onTime);                             // Add ISR Function
  
  /* Dividers:
    TIM_DIV1 = 0,   //80MHz (80 ticks/us - 104857.588 us max)
    TIM_DIV16 = 1,  //5MHz (5 ticks/us - 1677721.4 us max)
    TIM_DIV256 = 3  //312.5Khz (1 tick = 3.2us - 26843542.4 us max)
  Reloads:
    TIM_SINGLE  0 //on interrupt routine you need to write a new value to start the timer again
    TIM_LOOP  1 //on interrupt the counter will start with the same value again
  */
  
  timer1_enable(TIM_DIV16, TIM_EDGE, TIM_LOOP);               // Configure timer1  
  timer1_write(TIMER_TKS);                                    // Amount of timer ticks to generate period of 100us (10kHz).
  interrupts();                                               // Enable interruptions
  Serial.println(F("Timer 1 configured."));

  Serial.println(F("Configurations finished."));
  Toggle();
  Serial.print(F("Running with Tau = "));
  Serial.println(voo.tau,2);
}



/* ----- Main function definition ----- */

void loop() {
  
  // Read height and pressure
  float h = read_avg_BMP();
  voo.dt = get_dt();
  
  // Insert on arrays and do calculations
  voo.addAltura(h);
  
  // Save data to SD card
  save_to_SD(voo);

  switch(state){
    case 0:         // E1 = Initialization
    
      if (flight_condition()){
        Serial.println(F("E1 --> E2"));
        noInterrupts();
        timeLiftOff = timeCount;
        interrupts();
        state = 1;
      }
      break;
    case 1:         // E2 = Propulsive Flight
      if(burn_end_condition()){
        Serial.println(F("E2 --> E3"));
        state = 2;
      }
      break;
    case 2:         // E3 = Ballistic Flight
      if(apogee_condition()){
        Serial.println(F("E3 --> E4"));
        digitalWrite(IGN, LOW);    // Activate Ignition
        state = 3;
        delayCount = 0;
      }
      break;
    case 3:         // E4 = Parachute 
      if(delayCount > 1818){   // Wait for approximately 10s
        Serial.println(F("Deactivate ignitor."));
        digitalWrite(IGN, HIGH);                 // Deactivate Ignition
      }
      else if (voo.velocidadeF.getValor(0) > 10){                  // Re-activate Ignition if NC is still present (resistance unchanged)
        Serial.println(F("PROBLEM: Re-activate ignition!"));
        digitalWrite(IGN, LOW);
        delayCount = 0;
      }
      if(landing_condition()){
        Serial.println("E4 --> E5");
        state = 4;
      }
      break;
    case 4:         // E5 = Ground reached
      digitalWrite(IGN, HIGH);                 // Deactivate Ignition
      digitalWrite(BUZZ, HIGH);               // Activate Buzzer
      break;
    
    case 10:        // E11 = Failure mode
      Serial.println(F("Failure state!"));
      while(1){
        yield();
        // Continuous loop of buzzer beeps (1s)
        digitalWrite(BUZZ, HIGH);           // Activate Buzzer
        delay(1000);
        digitalWrite(BUZZ, LOW);            // De-activate Buzzer
        delay(1000);
      }
      return;
      break;
  }
}

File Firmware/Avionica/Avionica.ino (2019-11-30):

/***************************************************************************
  ------------- Embedded firmware for the Anhangá Rocket -----------------
  Authors: Batata, Joan, Gabriel
  Version: 0.3 - 26/11/2019 [Teste paraquedas CEPETRO]

  Description:
    This firmware implements a state machine, keeping track of the rocket
    flight phases and acting accordingly. 
    There are 5 main flight states:
      E1 - Ground before launch
      E2 - Propulsive flight
      E3 - Ballistic flight
      E4 - Descent with parachute
      E5 - Ground after flight
    Between each of these states, there are main transitions and actions 
    on the rocket, the parachute launch being the most important one.
    
    The rocket phases and state transitions, as well as the fluxogram of this
    code are presented in detail in the firmware development report, located 
    in Antares Google drive repository.
  
 ***************************************************************************/

/* ----- Library Inclusion ----- */

#include <Wire.h>
#include <Adafruit_BMP280.h>
#include <SD.h>
#include <SPI.h>
#include "voo.h"


/* ----- Macro definitions ----- */

#define IGN       (2)       // I/O pin for ignitor digital output
#define BUZZ      (8)       // I/O pin for buzzer digital output
#define IGN_READ  (A0)      // I/O pin for analogic ignitor read
#define ADD_BMP1  0x76      // Address of BMP no. 1
#define ADD_BMP2  0x77      // Address of BMP no. 2
#define CS_PIN    9         // Chip Select pin for SPI communication with SD card
#define TIMER_TKS 200       // Timer ticks in a period (Timer 1 runs at 2MHz freq.) - [200 for period of 0.1ms]
#define T_MEASURE 56        // Measure period (x 0.1ms) - [56 for 181.8 Hz]
#define LED_TEST  (13)      // Digital output pin for testing


/* ----- Type definitions ----- */

//typedef long long signed int BMP280_S64_t;
//typedef unsigned long int BMP280_U32_t;
//typedef signed long int BMP280_S32_t;


/* ----- Global variables definitions ----- */

const int chipSelect = CS_PIN;            // CS for SPI communication with SD card
volatile unsigned long timeCount = 0UL;   // A long is 32 bits long = 4294967296 levels
                                          // Using a dt=100us, it can count up to 119 hours
volatile int measureCount = 0;            // Counter for dividing timer freq. to get measure freq.
volatile byte state = 0;                  // State of the flight (E1 corresponds to 0, and so forth)
volatile bool led_on = false;             // Variable for test LED state

Adafruit_BMP280 bmp1, bmp2;               // Object used as BMP280 driver - I2C use
Voo voo1 = Voo(50);                       // Object containing height, velocity, acceleration - sensor 1
Voo voo2 = Voo(50);                       // Object containing height, velocity, acceleration - sensor 2
volatile unsigned long timeSave1 = 0UL;   // Variable used for storing moment of last measure of sensor 1
volatile unsigned long timeSave2 = 0UL;   // Variable used for storing moment of last measure of sensor 2
volatile float bmpPi1, bmpPi2;            // Initial pressures on sensors 1 and 2
volatile float bmpHi1, bmpHi2;            // Initial height measured on sensors 1 and 2
volatile float bmpD1, bmpD2;              // Derivative of height w.r.t. pressure on initial pressure 



/* ----- Auxiliary function definitions ----- */

/* Timer 1 Interruption Sub-Routine */
ISR(TIMER1_COMPA_vect){
  timeCount++;                    // Increments time counter
  measureCount++;                 // Increments measure counter
  if(measureCount == T_MEASURE)   // 5600us makes a period of 181.8Hz
    measureCount = 0;             // Reset measure counter for main program
}

/* Save data to SD function */
void save_to_SD(String bmp, Voo dados){
  File dataFile;                                        // Object used as SD driver - SPI use
  Serial.println(F("Dados de altura internos:"));
  int vsize = 4;
  float vect [vsize] = {timeCount/10000.0,              // Time since start-up in seconds
                        dados.altura.getValor(-1),      // Last acquired height measure [m]
                        dados.velocidade.getValor(-1),  // Last acquired velocity measure [m/s]
                        dados.aceleracao.getValor(-1)}; // Last acquired acceleration measure [m/s2]                     
  dataFile = SD.open("antares.txt", FILE_WRITE);
  if(!dataFile){
    Serial.println(F("---------> ERRO na abertura do arquivo"));
  }
  dataFile.print(bmp);
  Serial.print(bmp);
  for(int i=0; i<vsize; i++){
    dataFile.print("\t");
    dataFile.print(vect[i]);
    Serial.print("\t");
    Serial.print(vect[i],5);
  }
  dataFile.print("\n");
  Serial.print("\n");
  dataFile.close();
  return;
}

/* BMP height configuration - call on setup */
bool configure_BMP(byte bmp_nb){
  if(bmp_nb <=0 || bmp_nb >=3){
    Serial.println(F("ERROR: configure_BMP -> invalid BMP number!"));
    return(false);
  }
  float bmpPi = 0;
  float bmpHi = 0;
  float bmpDi = 0;
  int address = (bmp_nb == 1) ? ADD_BMP1 : ADD_BMP2;            // Gets bmp adress accordingly
  Adafruit_BMP280 * bmpHandle = (bmp_nb == 1) ? &bmp1 : &bmp2;  // Gets bmp object handle accordingly
  if (!bmpHandle->begin(address)) {                             // Initialize BMP
    Serial.print(F("Could not find BMP280 sensor (add="));
    Serial.print(address);
    Serial.println(F("), check wiring and reset!"));
    return(false);
  }
  bmpHandle->setSampling(Adafruit_BMP280::MODE_NORMAL,         /* Operating Mode. */
                  Adafruit_BMP280::SAMPLING_X2,               /* Temp. oversampling */
                  Adafruit_BMP280::SAMPLING_X16,              /* Pressure oversampling */
                  Adafruit_BMP280::FILTER_OFF,                /* Filtering. */
                  Adafruit_BMP280::STANDBY_MS_500);           /* Standby time. */
  for(int i=0; i<100; i++){
    bmpPi += bmpHandle->readPressure();                        // Read initial pressure
    bmpHi += bmpHandle->readAltitude();                        // Read initial altitude (exponential method)
  }
  bmpPi = bmpPi/100.0;                                        // Get average of pressure in 100 measures
  bmpHi = bmpHi/100.0;                                        // Get average of height in 100 measures
  bmpDi = -2260.209*pow(bmpPi,-0.8097);                       // Calculate derivative in initial pressure
  if (bmp_nb == 1){                                           // Save data in according variables
    bmpPi1 = bmpPi;
    bmpHi1 = bmpHi;
    bmpD1 = bmpDi; 
  }
  else{
    bmpPi2 = bmpPi;
    bmpHi2 = bmpHi;
    bmpD2 = bmpDi;
  }
  Serial.print(F("Finished configuration of BMP "));
  Serial.println(bmp_nb);
  Serial.print(F("bmpPi = "));
  Serial.println(bmpPi,3);
  Serial.print(F("bmpHi = "));
  Serial.println(bmpHi,3);
  Serial.print(F("bmpDi = "));
  Serial.println(bmpDi,3);
  return(true);
}
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

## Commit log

2019-10-24 Codigo para teste do BMP280 e SD
2019-11-05 Set sample bmp2
2019-11-22 Added Timer Interruption + Initialization + State Machine on loop().
2019-12-03 Filter implementation and most conditions for state machine - prototype
2019-12-04 Ejection test - filter and ignition corrected
    [Anhanga.ino]
2019-12-04 Ejection test - Ready for new board
2021-05-14 Added TODO for velocity decision considerations
2022-10-06 projeto de hardware desenvolvido para a placa Irapuru II
    [Avionica-B_Cu.gbr, Avionica-B_Mask.gbr, Avionica-B_Paste.gbr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]
2022-11-30 firmware para uso no ESP8266
